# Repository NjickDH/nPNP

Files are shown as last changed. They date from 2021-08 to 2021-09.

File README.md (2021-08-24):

# nPNP
Banner

## Description
This project will aim to build a high speed and accurate pick and place machine using bldc motors as servo's, automatic feeders and vision. Currently work is being done on developing component feeders.

## Features
- __Automatic component feeders:__
  - Designed for use of tape with 8mm Tape and Reel specifications.
  - Uses a 40x40mm aluminium profile as rail for mounting with integrated usb port for automatic powering and communication with the feeders.
  - Capable of accepting 20 feeders on a 500mm long aluminium profile.
  - SMT Reel holder which makes use of full sized reels convenient.
  - Handle for ease of insertion/removal from aluminium rail.
  - UART over RS485 for easy and reliable communication with the feeders. This means all feeders are controllable using a single USB port with use of a USB-RS485 converter.
  - Two buttons for manual control of the motor driving the tape forwards and backwards.
  - RGB Status LED provides the user with the current status of each feeder.
  - Integrated IR sensor as rotary encoder for accurate repeatability of the motors movement.
  - Automatically and mechanically peels tape based on the movement of the tape itself to reduce complexity and part count.
  - 
-

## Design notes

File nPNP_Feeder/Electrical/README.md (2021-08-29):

# nPNP Feeder electrical

## Description
The schematic and board files for all PCB's for each feeder are placed here. Please read relevant notes for each of these boards below.

## Notes
- __MainFeeder:__
  - Schematic has MCU named as ATmega328-AU as this is the highest MCU in the pin compatible series. Actual MCU in the main feeder, and for which the firmware is written, is the ATmega48A. For more information about pin compatibility click [here](https://ww1.microchip.com/downloads/en/DeviceDoc/ATmega48A-PA-88A-PA-168A-PA-328-P-DS-DS40002061B.pdf) .
- __USBFeeder:__
  - This PCB has to be connected to the main feeder PCB by soldering 4 wires from the 4 pads on the USBFeeder PCB to the 4 pads on the main feeder PCB.
- __ConnectorHolder:__
  - This PCB is to be inserted into the 40x40mm aluminium profile. Two holes on each end are used for mounting the PCB inside the slot. An alumium profile with the following dimensions must be used:
  <p align="center">
    
  </p>
  
### TODO:
- [x] Add BOM for each PCB
- [ ] Add price estimation for each PCB
- [ ] Validate MainFeederV1.0

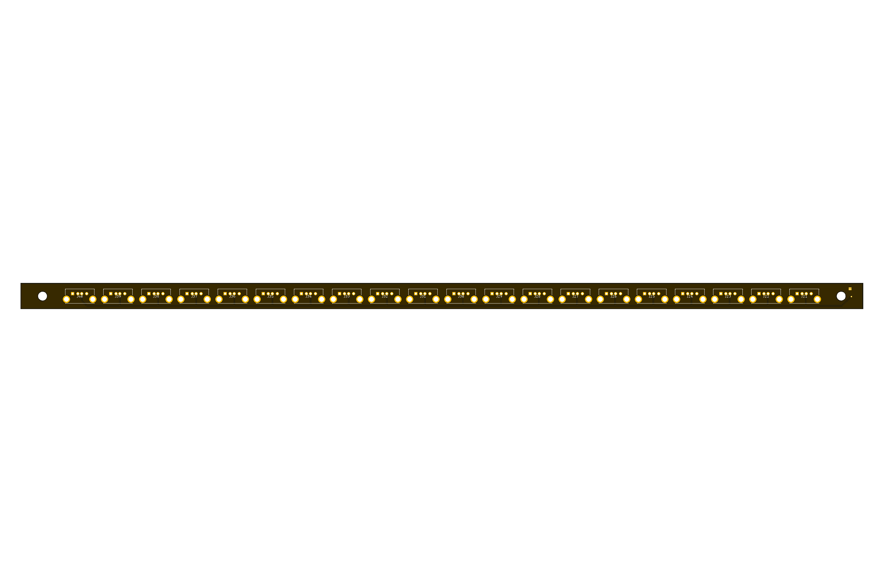
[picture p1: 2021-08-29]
nPNP_Feeder/Electrical/ConnectorHolder/ConnectorHolderPCB_V0.3_top.png

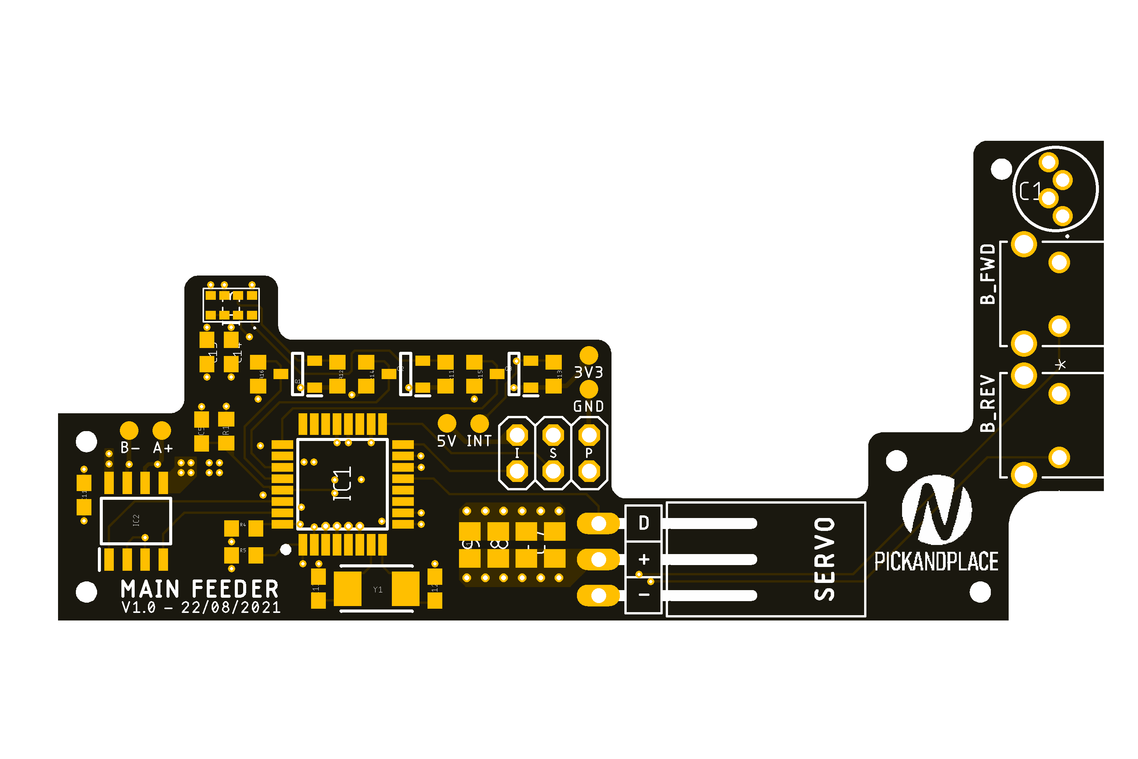
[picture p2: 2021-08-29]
nPNP_Feeder/Electrical/MainFeeder/MainFeeder_V1.0_top.png

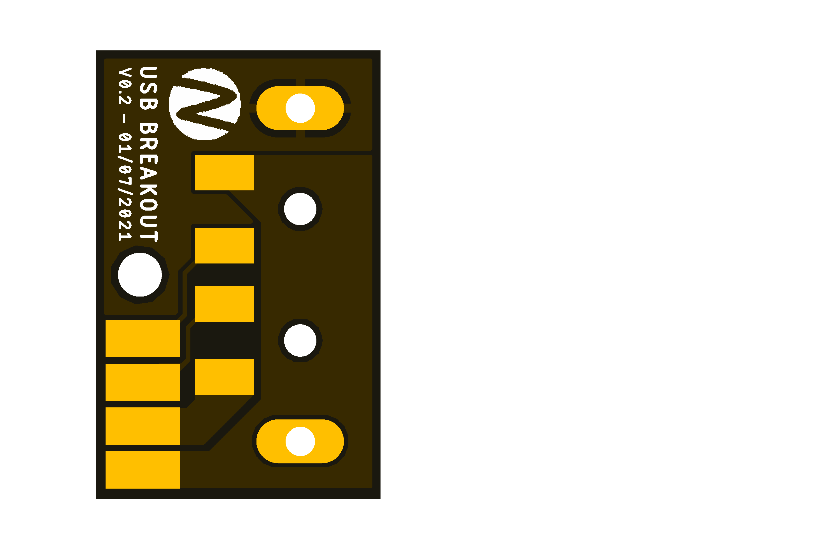
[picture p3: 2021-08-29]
nPNP_Feeder/Electrical/USBFeeder/USBFeederPCB_V0.2_top.png

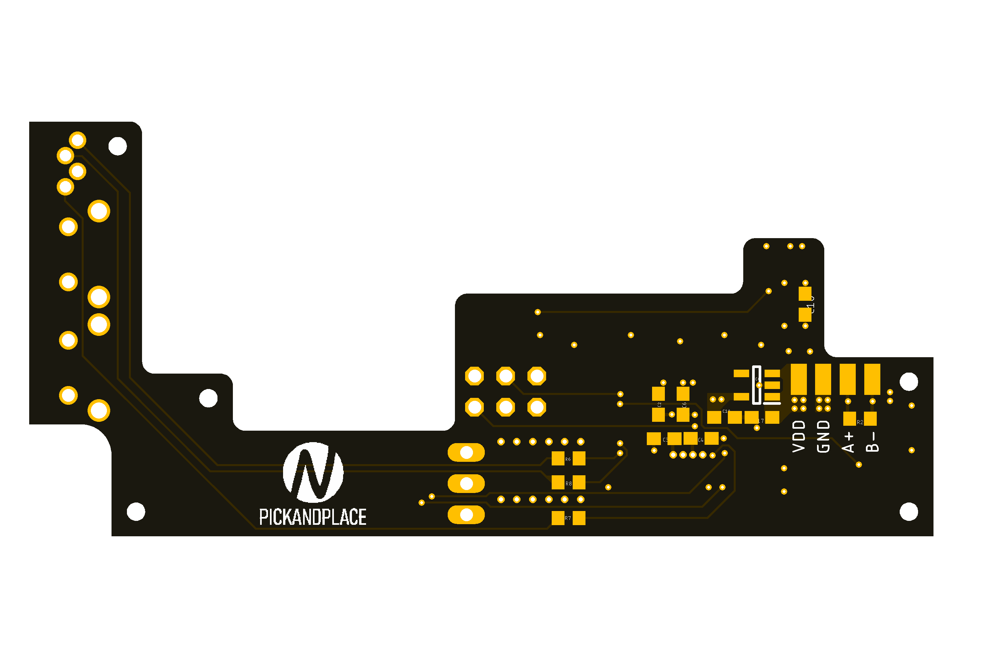
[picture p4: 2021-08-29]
nPNP_Feeder/Electrical/MainFeeder/MainFeeder_V1.0_bottom.png

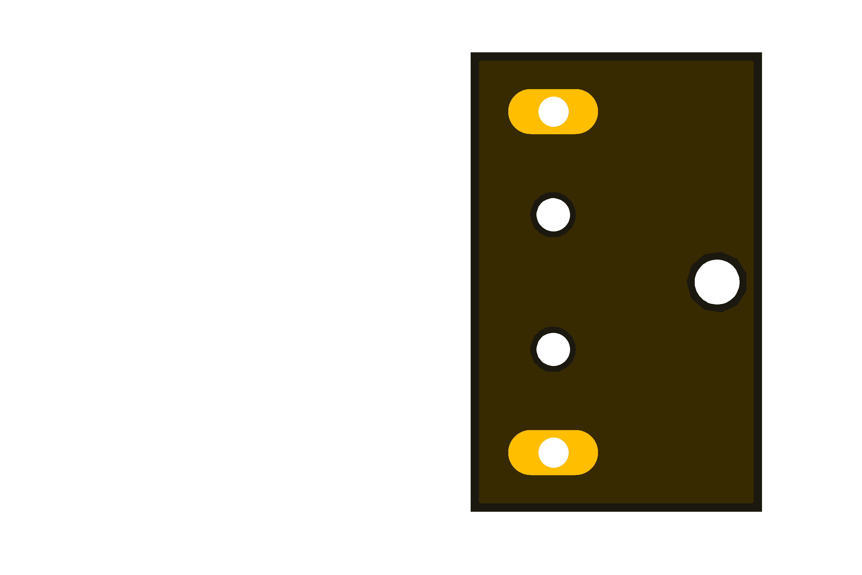
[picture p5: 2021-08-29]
nPNP_Feeder/Electrical/USBFeeder/USBFeederPCB_V0.2_bottom.png

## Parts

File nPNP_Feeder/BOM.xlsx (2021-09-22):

nPNP Feeder
Bill of materials of everything needed to build 20 nPNP Feeders and the feeder rail which the feeders connect into. Plastic price estimation is done using Cura. Some components are bought off of AliExpress but are based off of components made by more recognized manufacturers. Links are added altough these might expire. The BOM is split into two parts: Electrical and Hardware. Electrical will list all components to build the PCB's and the PCB's themselves. Hardware will list all bolts, 3D printed parts, servo's and aluminium parts needed.
Electrical
Component | Description | Manufacturer | Quantity | Price (EUR) | Link/Extra
Connector Holder
ConnectorHolder PCB | PCB with 20 USB A connectors; To be placed in 40x40mm aluminum profile | JLCPCB | 5 (Minimum) | 5.27
1734366-1 (Based on) | USB Type A connector - female | AliExpress | 20 | 2.34 | Link (https://nl.aliexpress.com/item/32809692203.html?spm=a2g0s.9042311.0.0.711b4c4drpQHzQ)
Total: |  |  |  | 7.61
Total/piece: |  |  |  | 0.3805
USB Feeder (Breakout board)
USBFeederPCB | PCB for a single USB Type A male connector with solder pads | JLCPCB | 30 | 3.74
480371000 (Based on) | USB Type A connector - male | AliExpress | 20 | 1.4 | Link (https://nl.aliexpress.com/item/32900067411.html?spm=a2g0s.9042311.0.0.711b4c4drpQHzQ)
Total: |  |  |  | 5.14
Total/piece: |  |  |  | 0.257
Main Feeder
MainFeeder_V1.0 | Main feeder PCB | JLCPCB | 20 | 38.76 | Incl. shipping to EU
PINHD-1X3/90 | 90 Degree pin header for servo | Generic | 20 | 1.44
FSMRA4JH04 | Tactile Switch SPST-NO Side Actuated Through Hole, Right Angle | TE Connectivity | 40 | 7.88
100nF/25V/0603 (C0603C104Z3V ) | Capacitor | Generic | 200 (Min. 120) | 2.2
47uF/6.3V/0805 (GRM21BR60J476M01L) | Capacitor | Generic | 100 (Min. 80) | 11.6
10K/100mW/0603 (RC0603JR-0710KL) | Resistor | Generic | 1000 (Min. 180) | 3
12pF/6.3V/0603 (C0603C120K9RAC7411) | Load capacitor | Generic | 100 (Min. 40) | 3
1uF/16V/0603 (EMK107BJ105MA-T) | Capacitor | Generic | 100 | 2.2
220/100mW/0603 ( CRCW0603220RJNEAC) | Resistor | Generic | 100 (Min. 20) | 1
560/100mW/0603 (ERJ-3EKF5600V) | Resistor | Generic | 100 | 1.1
ATMEGA48A-AUR | Microcontroller | Microchip | 20 | 28.2
BSS138 | MOSFET | onsemi | 60 | 11.58
ECS-160-12-30-AEM-TR | 16Mhz crystal oscillator | ECS | 20 | 12.46
LTR-559ALS-01 | IR Proximity sensor | Lite-On | 20 | 11.34
MAX485CSA+T (Based on) | RS485 Transciever | Maxim Integrated | 20 | 3 | Link (https://nl.aliexpress.com/item/4001094783917.html?spm=a2g0s.9042311.0.0.27424c4dNtDW3P)
NCP164CSN330T1G | 3.3V LDO | onsemi | 20 | 10.5
WP154A4SEJ3VBDZGC_CA (Based on) | RGB LED | Kingbright | 20 | 1.8 | Link (https://nl.aliexpress.com/item/32852334348.html?spm=a2g0s.9042311.0.0.12d74c4d18Hr8y)
Total: |  |  |  | 128.14
Total/piece: |  |  |  | 6.407
Total: |  |  |  | 140.89
Total/piece: |  |  |  | 7.0445
Hardware

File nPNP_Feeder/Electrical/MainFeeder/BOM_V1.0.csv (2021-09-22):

Qty | Value | Device | Package | Parts | Description
1 | Generic | PINHD-1X3/90 | 1X03/90 | JP1 | PIN HEADER
1 | Generic | PINHD-2X3 | 2X03 | JP2 | PIN HEADER
2 | 1-1825027-1 | 1-1825027-1 | SW2_1825027-A_TEC | SW1, SW2 | Button
6 | 100nF | C-EUC0603 | C0603 | C3, C4, C5, C6, C11, C16 | CAPACITOR, European symbol
4 | 100uF | C-EUC0805 | C0805 | C7, C8, C9, C10 | CAPACITOR, European symbol
9 | 10K | R-EU_R0603 | R0603 | R1, R4, R5, R11, R12, R13, R14, R15, R16 | RESISTOR, European symbol
2 | 12pF | C-EUC0603 | C0603 | C12, C13 | CAPACITOR, European symbol
5 | 1uF | C-EUC0603 | C0603 | C2, C14, C15, C17, C18 | CAPACITOR, European symbol
1 | 220 | R-EU_R0603 | R0603 | R2 | RESISTOR, European symbol
3 | 560 | R-EU_R0603 | R0603 | R6, R7, R8 | RESISTOR, European symbol
1 | ATMEGA328-AU | ATMEGA328-AU | QFP80P900X900X120-32N | IC1 | MCU 8-Bit AVR 32KB Flash 2.5/3.3/5V ATMEGA328-AU, 8 bit AVR Microcontroller 20MHz 32 kB Flash, 1 kB, 2 kB RAM, I2C 32-Pin TQFP
3 | BSS138 | BSS138 | SOT95P240X120-3N | Q1, Q2, Q3 | N-channel MOSFET,BSS138 0.2A 50V
1 | ECS-160-12-30-AEM-TR | ECS-160-12-30-AEM-TR | ECS1601230AEMTR | Y1 | ECX-53 SMD CRYSTAL
1 | LTR-559ALS-01 | LTR-559ALS-01 | LTR559ALS01 | IC3 | Light to Digital Converters Ambient Light Photo Sensor
1 | MAX485CSA+T | MAX485CSA+T | SOIC127P600X175-8N | IC2 | RS-422/RS-485 Interface IC Low-Power, Slew-Rate-Limited RS-485/RS-422 Transceivers
1 | NCP164CSN330T1G | NCP164CSN330T1G | SOT95P275X110-5N | IC4 | LDO Regulator Pos 3.3V 0.3A 5-Pin TSOP T/R
1 | WP154A4SEJ3VBDZGC_CA | WP154A4SEJ3VBDZGC_CA | L-154A4SUREQBFZGEC | C1 | Standard LEDs - Through Hole 5MM RGB LED

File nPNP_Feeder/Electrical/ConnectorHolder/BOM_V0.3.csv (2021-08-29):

Qty | Value | Device | Package | Parts | Description | DESCRIPTION | HEIGHT | MANUFACTURER_NAME | MANUFACTURER_PART_NUMBER | MOUSER_PART_NUMBER | MOUSER_PRICE-STOCK | POPULARITY
20 | 1734366-1 | 1734366-1 | 17343661 | J21, J22, J23, J24, J25, J26, J27, J28, J29, J30, J31, J32, J33, J34, J35, J36, J37, J38, J39, J40 | USB Connectors 1PORT 4POS VERT T/H USB 2.0 BLACK | USB Connectors 1PORT 4POS VERT T/H USB 2.0 BLACK | 15mm | TE Connectivity | 1734366-1 | 571-1734366-1 | https://www.mouser.co.uk/ProductDetail/TE-Connectivity/1734366-1?qs=Y377PMEofyC1I8%2FZakOHrA%3D%3D

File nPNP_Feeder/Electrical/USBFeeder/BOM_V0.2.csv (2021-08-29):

Qty | Value | Device | Package | Parts | Description
1 | 480371000 | 480371000 | 480371000 | U$1 | Male USB-A connector

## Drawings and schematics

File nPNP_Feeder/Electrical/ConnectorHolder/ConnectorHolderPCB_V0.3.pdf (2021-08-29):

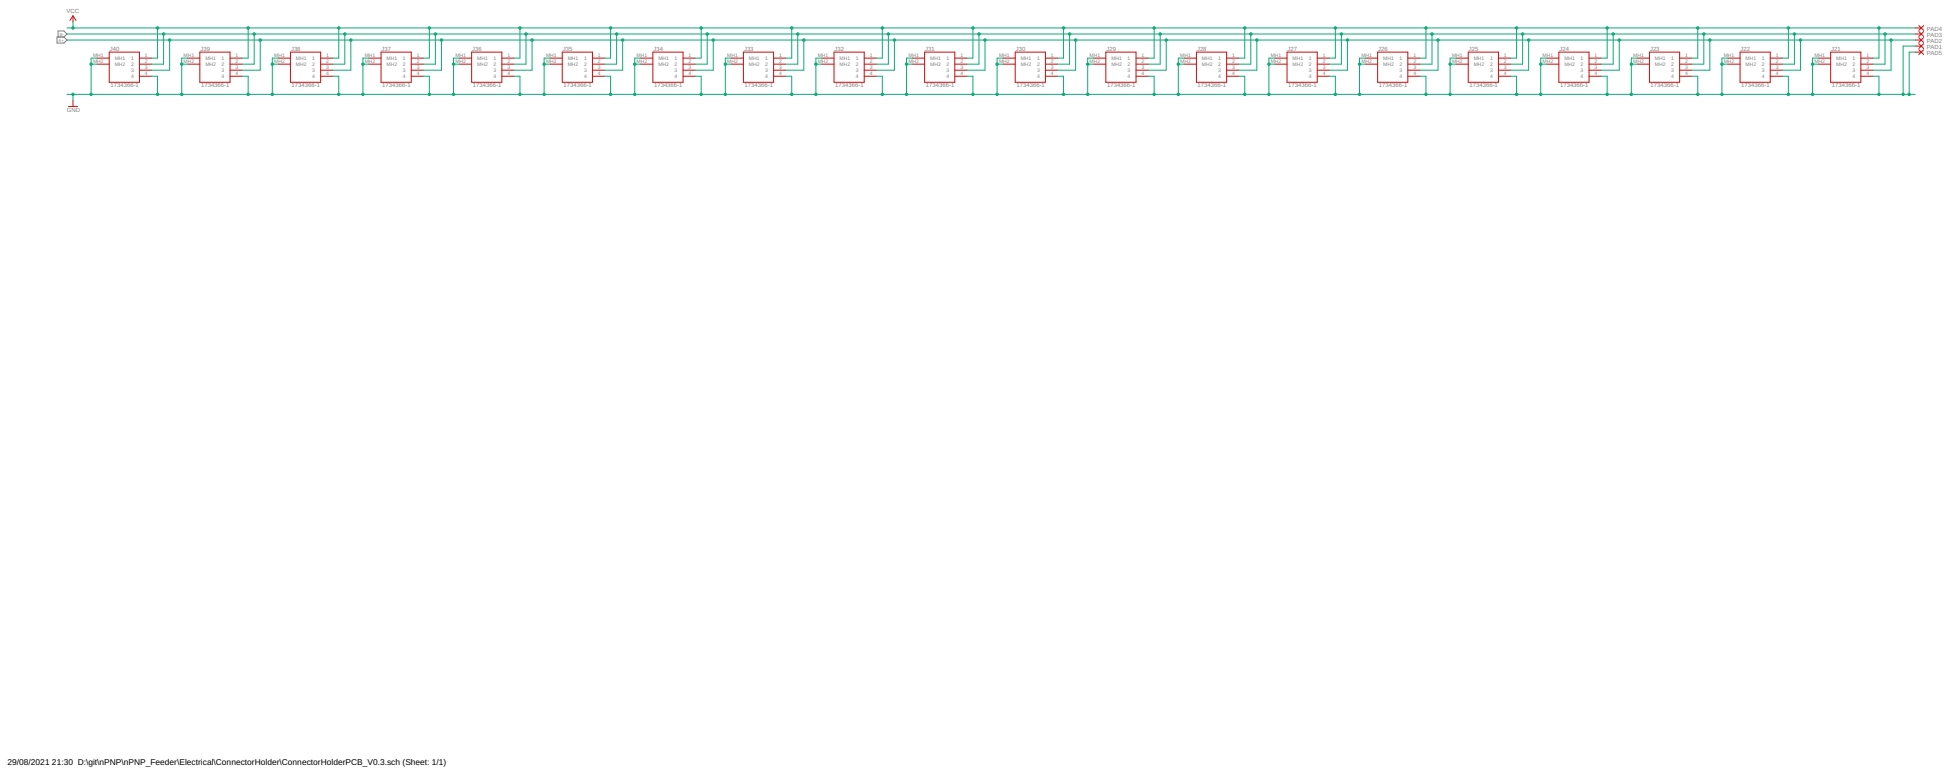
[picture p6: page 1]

29/08/2021 21:30 D:\git\nPNP\nPNP_Feeder\Electrical\ConnectorHolder\ConnectorHolderPCB_V0.3.sch (Sheet: 1/1)

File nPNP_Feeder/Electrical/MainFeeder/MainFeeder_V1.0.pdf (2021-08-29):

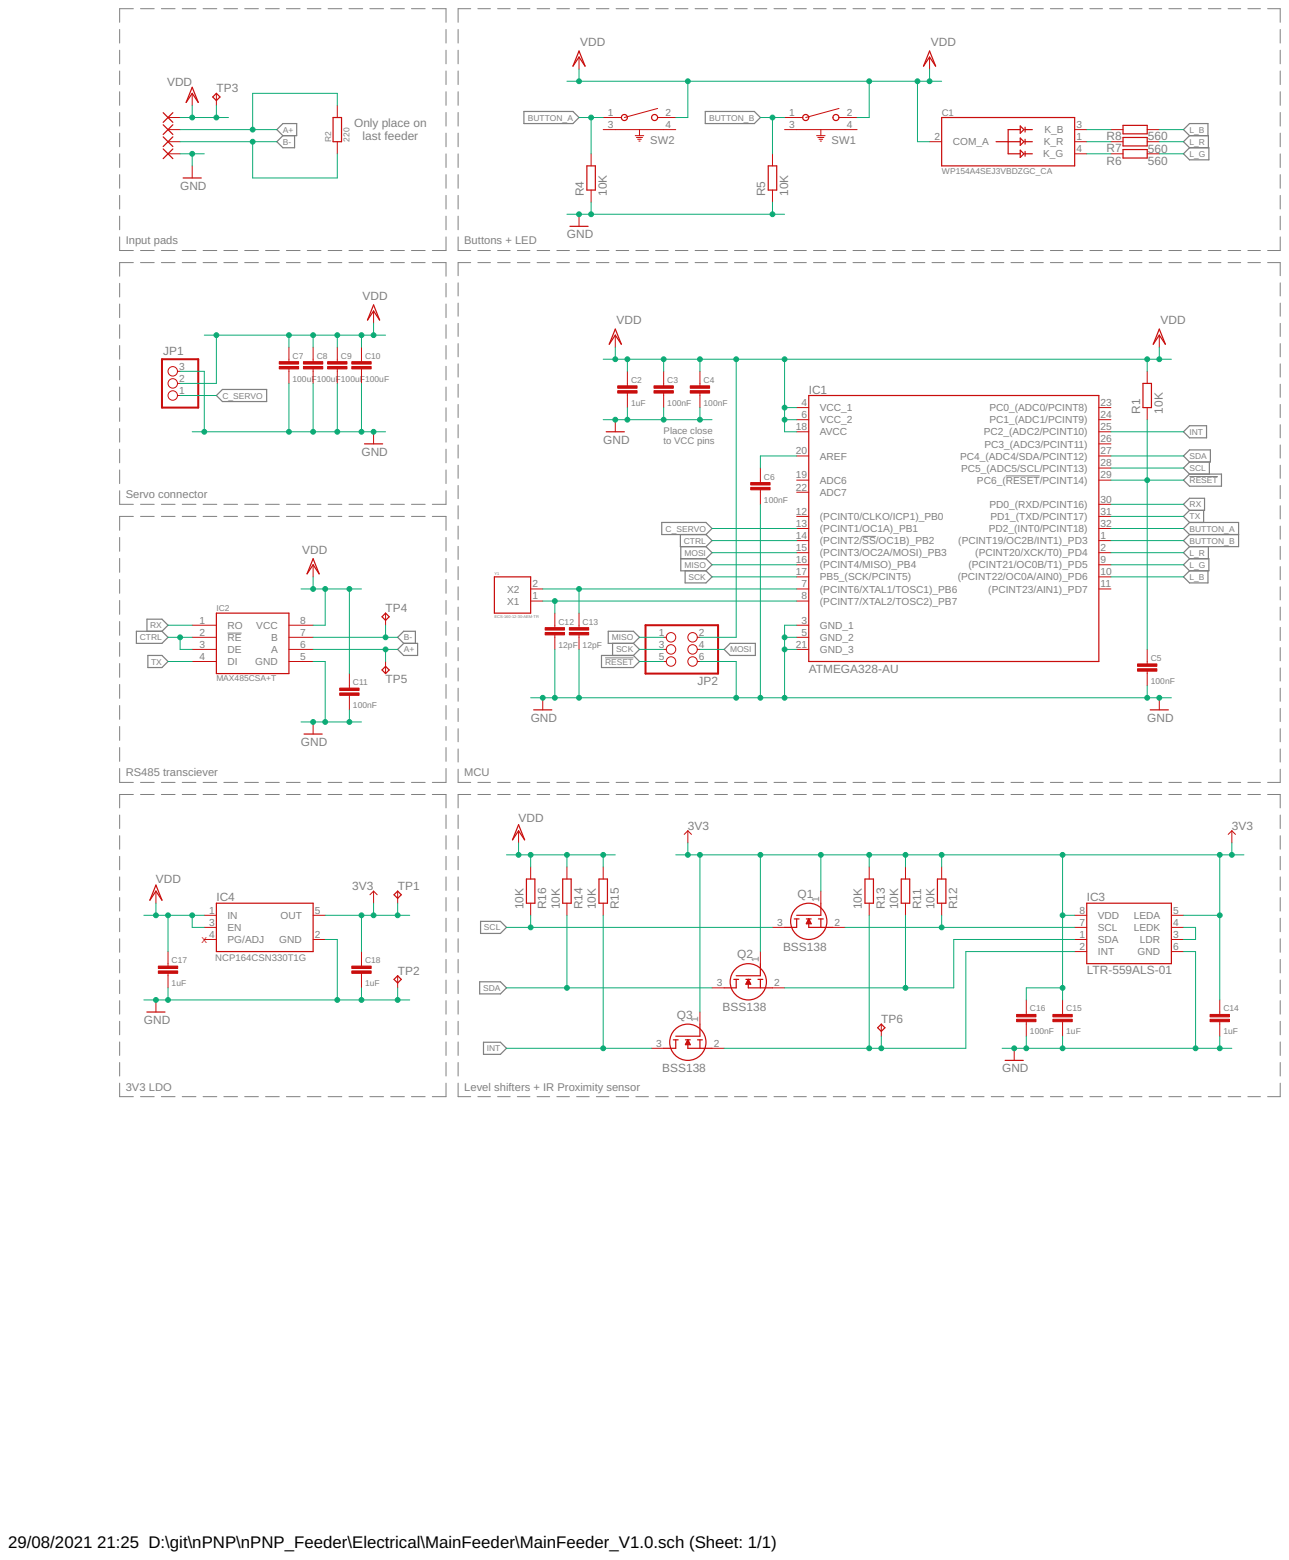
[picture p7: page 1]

29/08/2021 21:25 D:\git\nPNP\nPNP_Feeder\Electrical\MainFeeder\MainFeeder_V1.0.sch (Sheet: 1/1)

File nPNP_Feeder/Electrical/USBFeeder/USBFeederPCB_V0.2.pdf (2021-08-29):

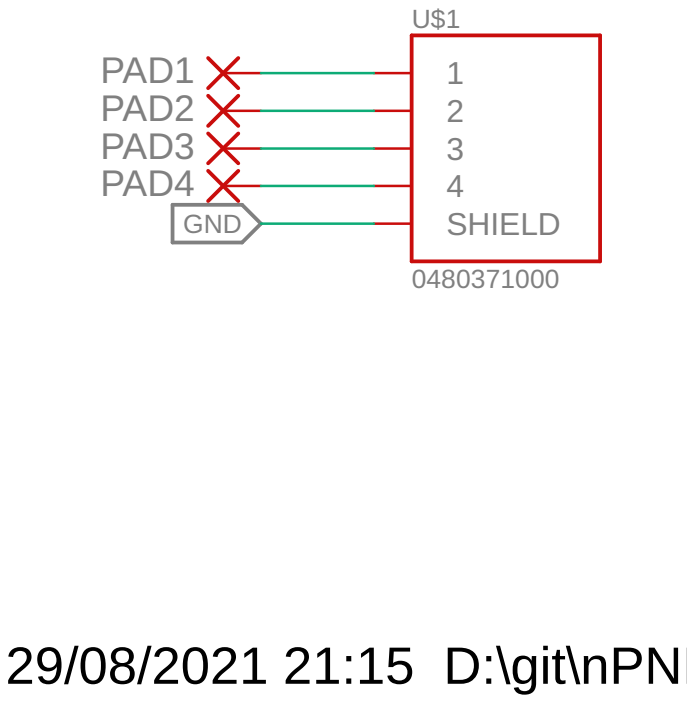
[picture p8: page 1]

29/08/2021 21:15 D:\git\nPNP\nPNP_Feeder\Electrical\USBFeeder\USBFeederPCB.sch (Sheet: 1/1)

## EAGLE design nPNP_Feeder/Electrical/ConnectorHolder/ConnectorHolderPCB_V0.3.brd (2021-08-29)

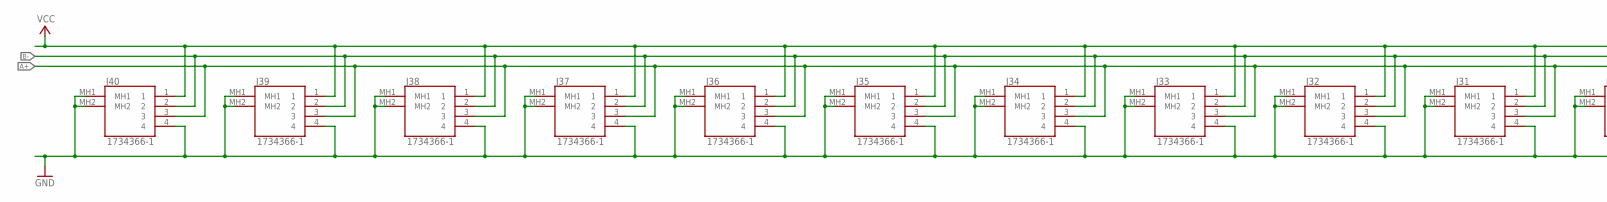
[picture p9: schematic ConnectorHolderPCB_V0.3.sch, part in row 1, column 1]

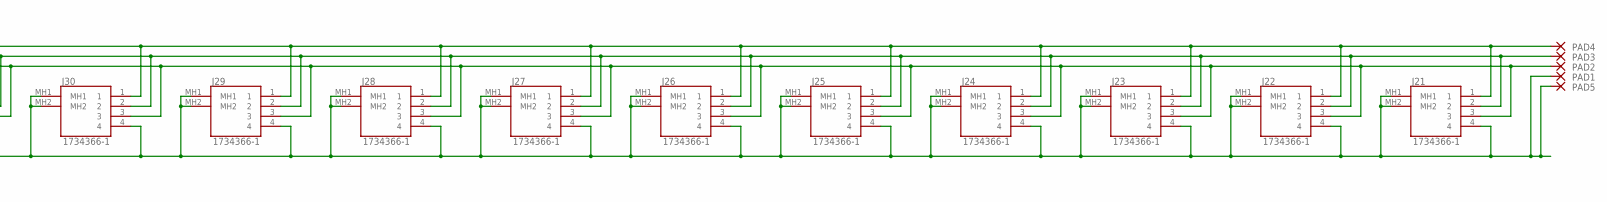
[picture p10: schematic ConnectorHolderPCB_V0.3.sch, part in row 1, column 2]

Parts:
J21, J22, J23, J24, J25, J26, J27, J28, J29, J30, J31, J32, J33, J34, J35, J36, J37, J38, J39, J40: 1734366-1; 17343661
PAD1, PAD2, PAD3, PAD4, PAD5: SMD2; SMD1,27-2,54

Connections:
A+: J21.3, J22.3, J23.3, J24.3, J25.3, J26.3, J27.3, J28.3, J29.3, J30.3, J31.3, J32.3, J33.3, J34.3, J35.3, J36.3, J37.3, J38.3, J39.3, J40.3, PAD2.1
B-: J21.2, J22.2, J23.2, J24.2, J25.2, J26.2, J27.2, J28.2, J29.2, J30.2, J31.2, J32.2, J33.2, J34.2, J35.2, J36.2, J37.2, J38.2, J39.2, J40.2, PAD3.1
GND: J21.4, J21.MH1, J21.MH2, J22.4, J22.MH1, J22.MH2, J23.4, J23.MH1, J23.MH2, J24.4, J24.MH1, J24.MH2, J25.4, J25.MH1, J25.MH2, J26.4, J26.MH1, J26.MH2, J27.4, J27.MH1, J27.MH2, J28.4, J28.MH1, J28.MH2, J29.4, J29.MH1, J29.MH2, J30.4, J30.MH1, J30.MH2, J31.4, J31.MH1, J31.MH2, J32.4, J32.MH1, J32.MH2, J33.4, J33.MH1, J33.MH2, J34.4, J34.MH1, J34.MH2, J35.4, J35.MH1, J35.MH2, J36.4, J36.MH1, J36.MH2, J37.4, J37.MH1, J37.MH2, J38.4, J38.MH1, J38.MH2, J39.4, J39.MH1, J39.MH2, J40.4, J40.MH1, J40.MH2, PAD1.1, PAD5.1
VCC: J21.1, J22.1, J23.1, J24.1, J25.1, J26.1, J27.1, J28.1, J29.1, J30.1, J31.1, J32.1, J33.1, J34.1, J35.1, J36.1, J37.1, J38.1, J39.1, J40.1, PAD4.1

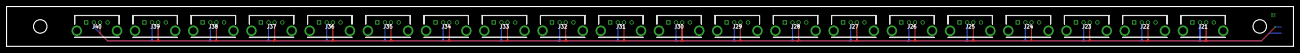
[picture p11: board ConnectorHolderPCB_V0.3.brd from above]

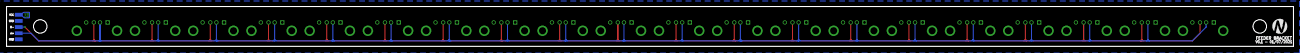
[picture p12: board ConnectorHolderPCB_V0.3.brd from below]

Board: 2 copper layers, 420.0 x 13.0 mm, 26 parts (6 on the bottom side), 4 nets.

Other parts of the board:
U$1: NPNP_LARGE_NOTEXT

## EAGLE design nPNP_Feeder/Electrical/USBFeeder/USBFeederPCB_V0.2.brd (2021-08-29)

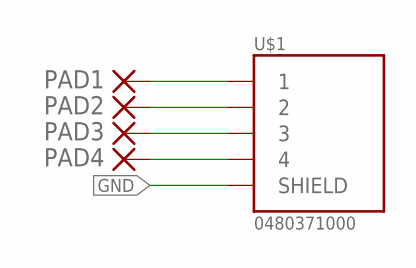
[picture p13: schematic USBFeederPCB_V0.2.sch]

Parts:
PAD1, PAD2, PAD3, PAD4: SMD2; SMD1,27-2,54
U$1: 0480371000

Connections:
GND: U$1.SHIELD1 (SHIELD), U$1.SHIELD2 (SHIELD)
unnamed: PAD1.1, U$1.1
unnamed: PAD2.1, U$1.2
unnamed: PAD3.1, U$1.3
unnamed: PAD4.1, U$1.4

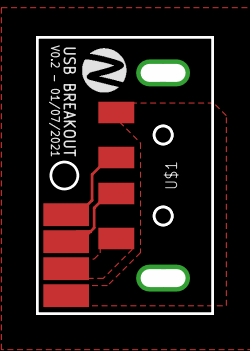
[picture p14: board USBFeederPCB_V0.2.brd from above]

Board: 2 copper layers, 9.7 x 15.3 mm, 6 parts (0 on the bottom side), 5 nets.

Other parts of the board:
U$3: NPNP_SMALL_NOTEXT

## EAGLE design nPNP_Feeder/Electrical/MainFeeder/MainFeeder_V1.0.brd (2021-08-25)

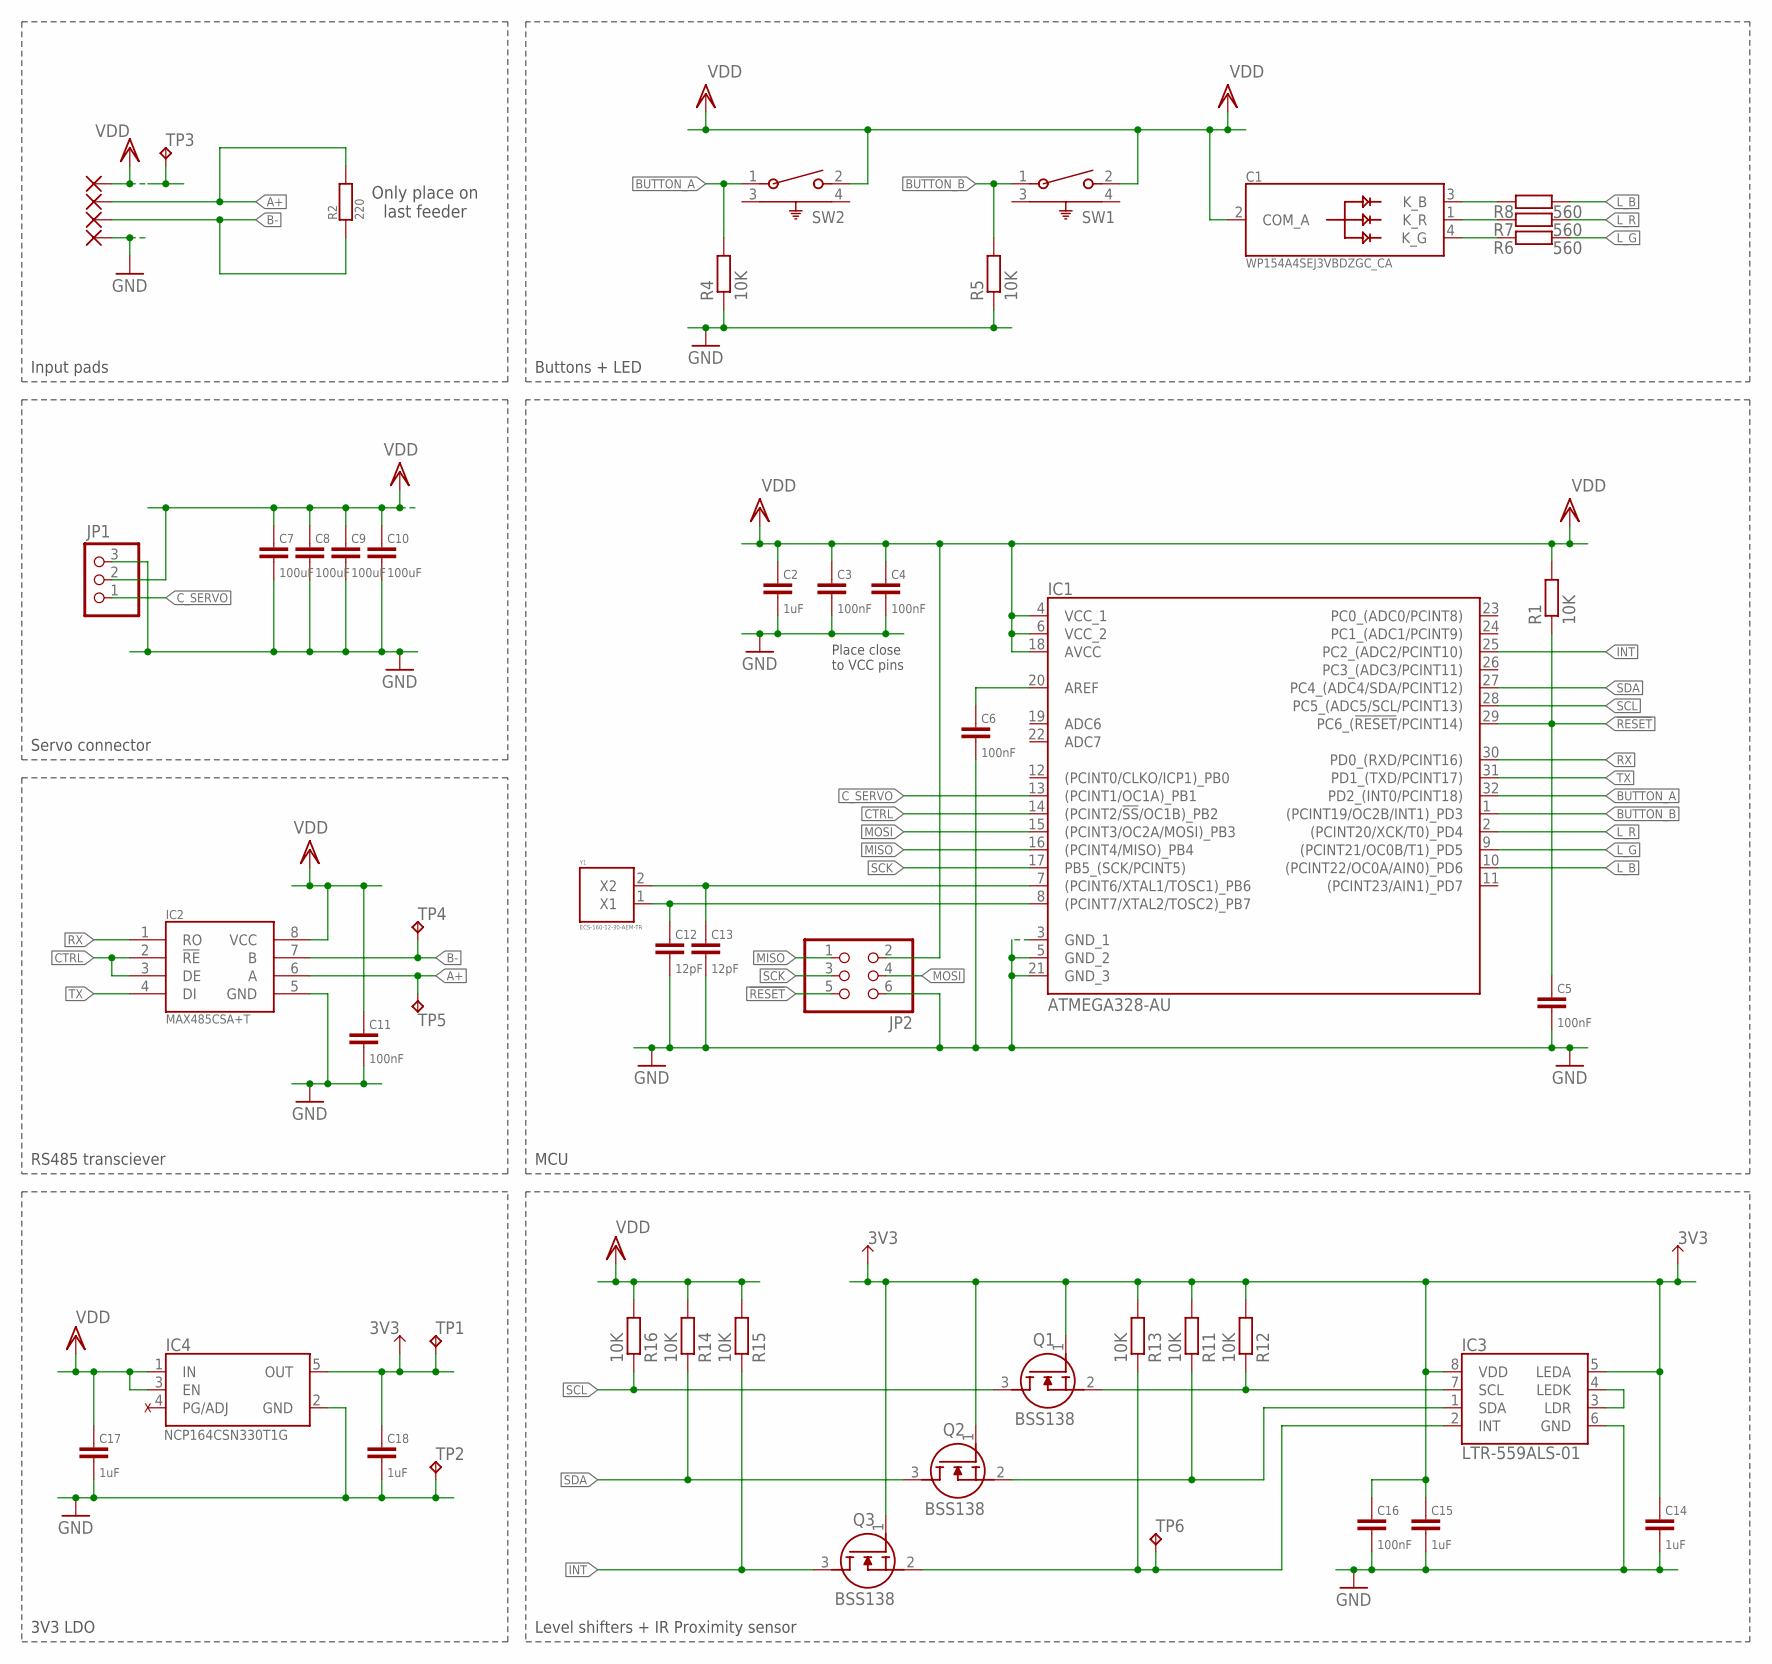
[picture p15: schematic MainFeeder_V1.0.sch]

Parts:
C1: WP154A4SEJ3VBDZGC_CA; L-154A4SUREQBFZGEC
C2, C14, C15, C17, C18: 1uF; C0603
C3, C4, C5, C6, C11, C16: 100nF; C0603
C7, C8, C9, C10: 100uF; C0805
C12, C13: 12pF; C0603
IC1: ATMEGA328-AU; QFP80P900X900X120-32N
IC2: MAX485CSA+T; SOIC127P600X175-8N
IC3: LTR-559ALS-01; LTR559ALS01
IC4: NCP164CSN330T1G; SOT95P275X110-5N
JP1: PINHD-1X3/90; 1X03/90
JP2: PINHD-2X3; 2X03
PAD1, PAD2, PAD3, PAD4: SMD2; SMD1,27-2,54
Q1, Q2, Q3: BSS138; SOT95P240X120-3N
R1, R4, R5, R11, R12, R13, R14, R15, R16: 10K; R0603
R2: 220; R0603
R6, R7, R8: 560; R0603
SW1, SW2: 1-1825027-1; SW2_1825027-A_TEC
TP1, TP2, TP3, TP4, TP5, TP6: TPB1,27; B1,27
Y1: ECS-160-12-30-AEM-TR; ECS1601230AEMTR

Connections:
3V3: C14.1, C15.1, C16.1, C18.1, IC3.5 (LEDA), IC3.8 (VDD), IC4.5 (OUT), Q1.1 (G), Q2.1 (G), Q3.1 (G), R11.2, R12.2, R13.2, TP1.TP
!RESET: C5.1, IC1.29 (PC6_(!RESET!/PCINT14)), JP2.5, R1.1
A+: IC2.6 (A), PAD1.1, R2.2, TP5.TP
B-: IC2.7 (B), PAD2.1, R2.1, TP4.TP
BUTTON_A: IC1.32 (PD2_(INT0/PCINT18)), R4.2, SW2.1
BUTTON_B: IC1.1 ((PCINT19/OC2B/INT1)_PD3), R5.2, SW1.1
CTRL: IC1.14 ((PCINT2/!SS!/OC1B)_PB2), IC2.2 (!RE), IC2.3 (DE)
C_SERVO: IC1.13 ((PCINT1/OC1A)_PB1), JP1.1
GND: C2.2, C3.2, C4.2, C5.2, C6.2, C7.2, C8.2, C9.2, C10.2, C11.2, C12.2, C13.2, C14.2, C15.2, C16.2, C17.2, C18.2, IC1.3 (GND_1), IC1.5 (GND_2), IC1.21 (GND_3), IC2.5 (GND), IC3.6 (GND), IC4.2 (GND), JP1.3, JP2.6, PAD3.1, R4.1, R5.1, TP2.TP
INT: IC1.25 (PC2_(ADC2/PCINT10)), Q3.3 (D), R15.1
INT_3V3: IC3.2 (INT), Q3.2 (S), R13.1, TP6.TP
L_B: IC1.10 ((PCINT22/OC0A/AIN0)_PD6), R8.1
L_G: IC1.9 ((PCINT21/OC0B/T1)_PD5), R6.1
L_R: IC1.2 ((PCINT20/XCK/T0)_PD4), R7.1
MISO: IC1.16 ((PCINT4/MISO)_PB4), JP2.1
MOSI: IC1.15 ((PCINT3/OC2A/MOSI)_PB3), JP2.4
unnamed: C6.1, IC1.20 (AREF)
unnamed: C1.3 (K_B), R8.2
unnamed: C1.1 (K_R), R7.2
unnamed: IC3.3 (LDR), IC3.4 (LEDK)
unnamed: C12.1, IC1.8 ((PCINT7/XTAL2/TOSC2)_PB7), Y1.1 (X1)
unnamed: C1.4 (K_G), R6.2
unnamed: C13.1, IC1.7 ((PCINT6/XTAL1/TOSC1)_PB6), Y1.2 (X2)
RX: IC1.30 (PD0_(RXD/PCINT16)), IC2.1 (RO)
SCK: IC1.17 (PB5_(SCK/PCINT5)), JP2.3
SCL: IC1.28 (PC5_(ADC5/SCL/PCINT13)), Q1.3 (D), R16.1
SCL_3V3: IC3.7 (SCL), Q1.2 (S), R12.1
SDA: IC1.27 (PC4_(ADC4/SDA/PCINT12)), Q2.3 (D), R14.1
SDA_3V3: IC3.1 (SDA), Q2.2 (S), R11.1
TX: IC1.31 (PD1_(TXD/PCINT17)), IC2.4 (DI)
VDD: C1.2 (COM_A), C2.1, C3.1, C4.1, C7.1, C8.1, C9.1, C10.1, C11.1, C17.1, IC1.4 (VCC_1), IC1.6 (VCC_2), IC1.18 (AVCC), IC2.8 (VCC), IC4.1 (IN), IC4.3 (EN), JP1.2, JP2.2, PAD4.1, R1.2, R14.2, R15.2, R16.2, SW1.2, SW2.2, TP3.TP

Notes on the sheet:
Input pads
Servo connector
Buttons + LED
Place close to VCC pins
MCU
RS485 transciever
Only place on last feeder
3V3 LDO
Level shifters + IR Proximity sensor

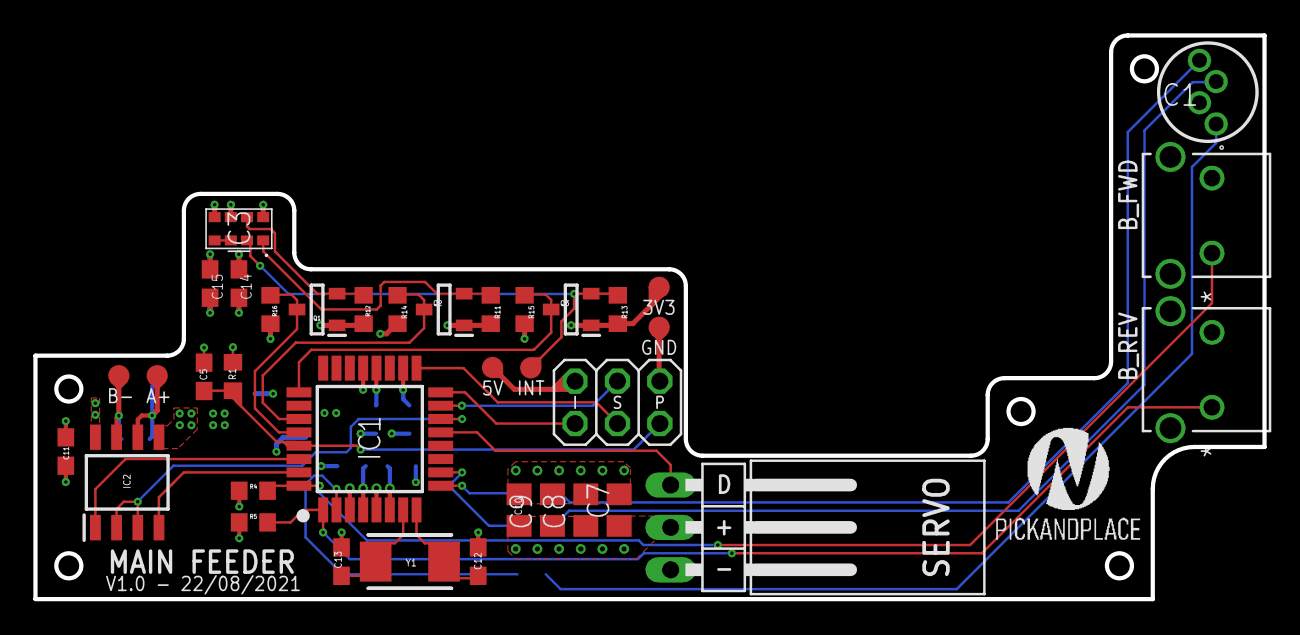
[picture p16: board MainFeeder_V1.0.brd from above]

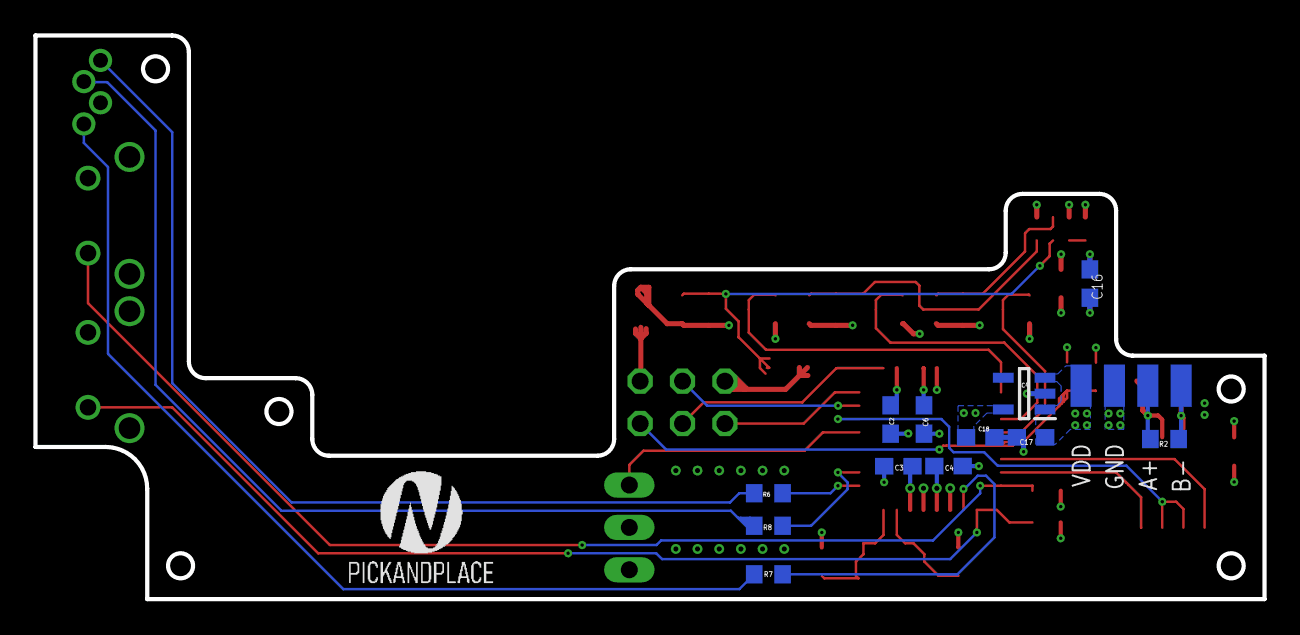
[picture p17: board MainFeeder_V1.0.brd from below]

Board: 4 copper layers, 73.7 x 33.8 mm, 55 parts (17 on the bottom side), 31 nets.

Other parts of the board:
U$2, U$3: NPNP_LARGE_TEXT

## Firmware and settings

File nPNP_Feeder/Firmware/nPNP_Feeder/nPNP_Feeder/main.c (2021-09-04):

/*
 * nPNP Feeder software
 *
 * Created: 13/08/2021 16:45:48
 * Author : Nick
 */ 

#include "board.h"
#include "RS485.h"
#include "servo.h"
#include "LTR559.h"
#include <avr/io.h>
#include <avr/interrupt.h>
#include <util/delay.h>

extern volatile uint8_t uartData;
int main(void)
{
	Board_init();		
	Timer_init();
	RS485_init();
	LTR559_Init();
	
	sei(); //Enable interrupts
	
    while (1) 
    {		
		switch(uartData)
		{
			case 'f':
				OCR1A = 2287;
				uartData = 0;
				break;
			case 'b':
				OCR1A = 2339;
				uartData = 0;	
				break;
		}

		while((PIND & (1 << BUTTON_A)) == (1 << BUTTON_A))
		{
			OCR1A = 2287;
			_delay_ms(100);
		}
		
		while((PIND & (1 << BUTTON_B)) == (1 << BUTTON_B))
		{
			OCR1A = 2339;
			_delay_ms(100);
 		}
	}
}

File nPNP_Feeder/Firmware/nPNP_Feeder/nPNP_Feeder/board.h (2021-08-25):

#ifndef BOARD_HEADER
#define BOARD_HEADER

#define F_CPU 16000000UL

#define BUTTON_A	PIND2
#define BUTTON_B	PIND3

#define LED_R		PD4
#define LED_B		PD5
#define LED_G		PD6

#define RS485_DE	PINB2

void Error_Handler();
void Board_init();

#endif

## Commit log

2021-08-25 Feeder schematic and board files
    [ConnectorHolderPCB_V0.3.brd, ConnectorHolderPCB_V0.3.sch, MainFeederV1.0.brd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]
2021-08-29 Added BOM, schematic as pdf and PCB as image
    [BOM_V0.2.csv, BOM_V0.3.csv, BOM_V1.0.csv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]
2021-09-04 POC of PWM with IR encoder feedback
2021-09-22 Global BOM start and BOM for MainFeederV1.0
    [BOM.xlsx, BOM_V1.0.csv]

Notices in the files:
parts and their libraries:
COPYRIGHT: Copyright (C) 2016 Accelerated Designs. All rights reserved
